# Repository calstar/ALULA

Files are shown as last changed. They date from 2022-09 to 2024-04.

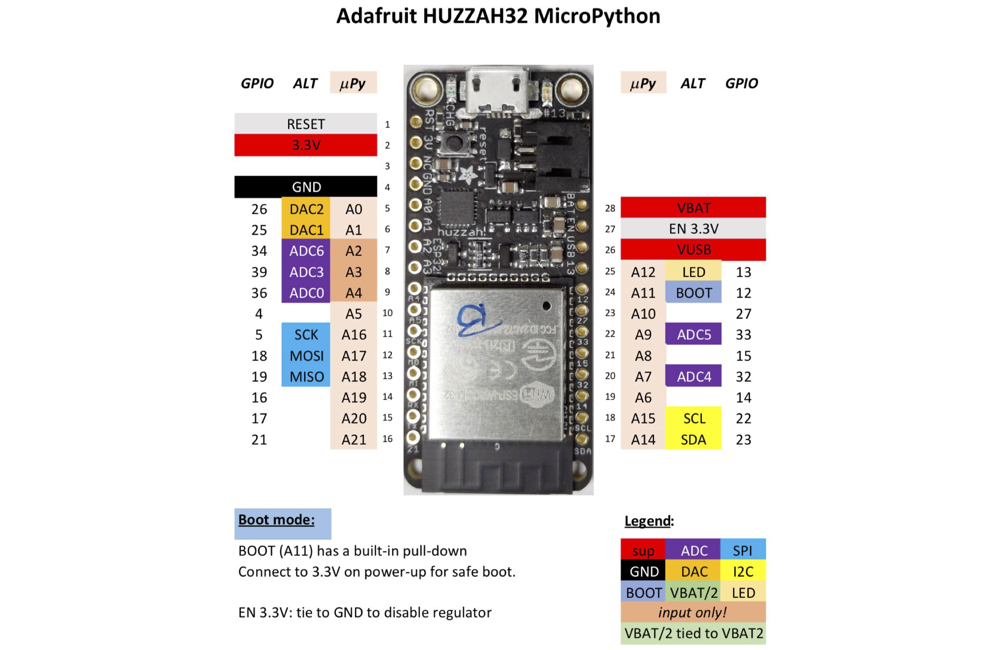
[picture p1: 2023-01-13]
esp32-huzzah-pinout.png

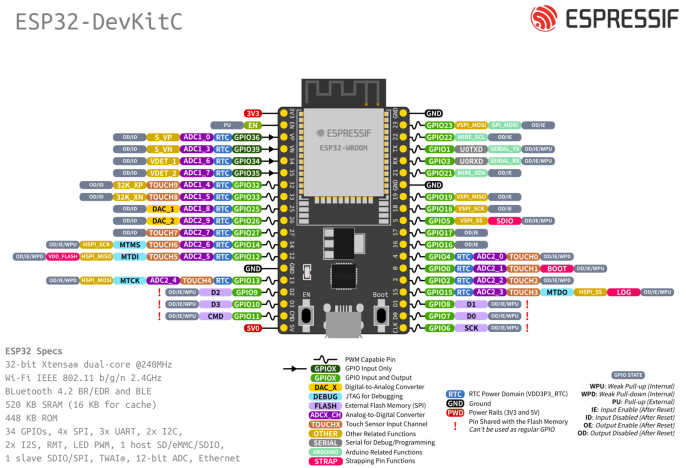
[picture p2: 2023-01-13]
SPRING-HOTFIRE-HARDWARE/le2_pcb/esp32-devkitC-v4-pinout.png

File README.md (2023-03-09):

# ALULA (LE2)
 Alula/ LE2 Hot-fire and Flight Vehicle Electronics Control

## Summary
**DAQboard.ino** file commands the ESP32 that reads data from sensors and commands from the COM Board, and sends data in a package to the COM Board.

**COMBoard.ino** file commands the ESP32 that receives data in a package from the DAQ  Board, sends commands to the DAQ Board, and sends data to MATLAB for plotting and data-saving purposes through the serial port.

**liveplot.m** is a MATLAB file that can receive data from the COM Board, create live plots, and save the data.
  1. **Change the test file name according to the trial number in the liveplot.m file.**
  2. Click "Run" to start the code, and close the plotting window to stop the code. Test data will be automatically stored in a spreadsheet under a folder called "**Test_Data_yyyy-mm-dd**."

## ESP32 MAC Addresses
- DAQ Breadboard:{0x24, 0x62, 0xAB, 0xD2, 0x85, 0xDC}
- COM Breadboard:{0xC4, 0xDD, 0x57, 0x9E, 0x91, 0x6C};
- DAQ Protoboard:

## Software requirement
**Ctrl click (Windows) or Cmd click the following links to open them in new tabs**
1. Arduino (https://www.arduino.cc/en/software)
2. MATLAB (https://software.berkeley.edu/matlab®)
    - To control the serial port, you need to install the [**Instrument Control Toolbox**](https://www.mathworks.com/products/instrument.html).
3. (optional) An external code editing software such as Atom (https://atom.io) or Visual Studio (https://visualstudio.microsoft.com/downloads/).
    - Arduino IDE and MATLAB are sufficient for all the coding
4. (recommended) GitHub Desktop (https://desktop.github.com). You can pull, push, and edit files with ease. **Step 3 required if you would like to download GitHub Desktop as the software requires an external editor.**

## How to contribute

### Using Git (recommended)
CLONE USING: 
```git clone --recurse-submodules git@github.com:calstar/LE2.git``` 

Please refer to https://rocketry.gitbook.io/public/tutorials/avionics/git-and-workflow for more information.

A basic workflow might go as follows:

`git status` 

`git add .` 

`git status` Note: if you see files here that are not code/hardware and should not be added (binaries, images, autosave files, etc.), STOP and fix the `.gitignore` 

`git commit -m "[Descriptive commit message of what you changed]"` 

`git push` 

### Using Github Desktop (not recommended)
1. Make sure you have access to this project
    - Check with you administrators
2. Go to the Github app, sign in, and click on the top left corner. You should see a pop-up window with an "Add" button. Select that button and choose "Clone repository."
3. Search in "Filter you repositories" using the keyword "ellie-ground." Select the correct repository and click "Clone."
    - If you want this cloned repository to be in a different folder, change the "Local Path."
4. After you have edited and saved the file in the local repository, GitHub Desktop will detect changes and prompt you to commit. Make sure to double check your changes before committing.
5. On the bottom left corner, put down a short summary that describes what you have changed, then click "Commit to **main**."
6. In the middle of the screen (or on the top banner) you will see "Push commits to the origin remote." If you are sure that the commit is ready, click "Push origin."
6. Check the project online and see if the changes have been reflected.

## Helpful resources
### ESP32-DevkitC/ ESP32-Devkit-v4 (for PCB application - antenna sticks out of board)
Getting started

https://docs.espressif.com/projects/esp-idf/en/latest/esp32/hw-reference/esp32/get-started-devkitc.html

Pinout reference

![esp32 devkitC pinout](https://github.com/calstar/ellie-ground/blob/main/Misc_resources/esp32-devkitC-v4-pinout.png?raw=true "ESP32 DevkitC Pinout")

### ESP32-WROOM/ ESP32-Devkit-v1 (for breadboard/protoboard application - antenna does NOT stick out of board)

Pinout reference
![esp32 wroom pinout](https://www.mischianti.org/wp-content/uploads/2020/11/ESP32-DOIT-DEV-KIT-v1-pinout-mischianti.png)

### ESP32-HUZZAH (for breadboard/protoboard application)

Pinout reference
![esp32 devkitC pinout](https://github.com/calstar/ellie-ground/blob/main/Misc_resources/esp32-huzzah-pinout.png?raw=true "ESP32 HUZZAH Pinout")

### Pressure transducer color code
Red - E+

Black - E-

Green - A-

White - A+

Other possible combinations: Blue E+; Red E-; Green A-; Black A+

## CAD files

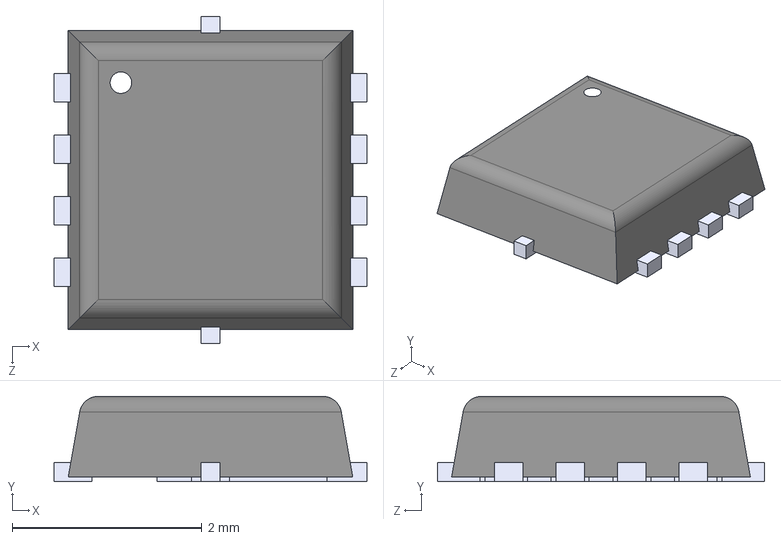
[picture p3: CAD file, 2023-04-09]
SPRING-HOTFIRE-HARDWARE/hotfire_pcbs/CSD25402Q3AT/CSD25402Q3AT.step
3.30 x 0.9 x 3.45 mm

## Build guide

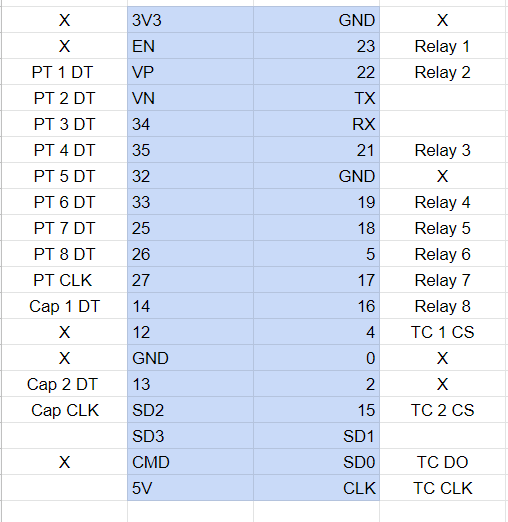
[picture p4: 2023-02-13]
SPRING-HOTFIRE-HARDWARE/le2_pcb/PROTOBOARDS/Core Board Setup.png

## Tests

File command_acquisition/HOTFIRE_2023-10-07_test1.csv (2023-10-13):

load:0x3fff0030,len:1344
load:0x40078000,len:13964
load:0x40080400,len:3600
entry | 0x400805f0
Start | of | Setup
274 | -1.00 | -1.00 | -1.00 | 0.00 | -1.00 | -1.00 | -1.00 | -1.00 | -1.00 | -1.00 | 0 | 0 | 1
526 | -1.00 | -1.00 | -1.00 | 0.00 | -1.00 | -1.00 | -1.00 | -1.00 | -1.00 | -1.00 | 0 | 0 | 1
777 | -1.00 | -1.00 | -1.00 | 0.00 | -1.00 | -1.00 | -1.00 | -1.00 | -1.00 | -1.00 | 0 | 0 | 1
1030 | -1.00 | -1.00 | -1.00 | 0.00 | -1.00 | -1.00 | -1.00 | -1.00 | -1.00 | -1.00 | 0 | 0 | 1
1283 | -1.00 | -1.00 | -1.00 | 0.00 | -1.00 | -1.00 | -1.00 | -1.00 | -1.00 | -1.00 | 0 | 0 | 1
1534 | -1.00 | -1.00 | -1.00 | 0.00 | -1.00 | -1.00 | -1.00 | -1.00 | -1.00 | -1.00 | 0 | 0 | 1
1787 | -1.00 | -1.00 | -1.00 | 0.00 | -1.00 | -1.00 | -1.00 | -1.00 | -1.00 | -1.00 | 0 | 0 | 1
2039 | -1.00 | -1.00 | -1.00 | 0.00 | -1.00 | -1.00 | -1.00 | -1.00 | -1.00 | -1.00 | 0 | 0 | 1
2290 | -1.00 | -1.00 | -1.00 | 0.00 | -1.00 | -1.00 | -1.00 | -1.00 | -1.00 | -1.00 | 0 | 0 | 1
2543 | -1.00 | -1.00 | -1.00 | 0.00 | -1.00 | -1.00 | -1.00 | -1.00 | -1.00 | -1.00 | 0 | 0 | 1
2795 | -1.00 | -1.00 | -1.00 | 0.00 | -1.00 | -1.00 | -1.00 | -1.00 | -1.00 | -1.00 | 0 | 0 | 1
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

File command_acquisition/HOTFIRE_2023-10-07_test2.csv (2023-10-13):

d:0x3fff0030,len:1344
entry | 0x400805f0
Start | of | Setup
283 | -1.00 | -1.00 | -1.00 | 0.00 | -1.00 | -1.00 | -1.00 | -1.00 | -1.00 | -1.00 | 0 | 0 | 1
535 | -1.00 | -1.00 | -1.00 | 0.00 | -1.00 | -1.00 | -1.00 | -1.00 | -1.00 | -1.00 | 0 | 0 | 1
787 | -1.00 | -1.00 | -1.00 | 0.00 | -1.00 | -1.00 | -1.00 | -1.00 | -1.00 | -1.00 | 0 | 0 | 1
1040 | -1.00 | -1.00 | -1.00 | 0.00 | -1.00 | -1.00 | -1.00 | -1.00 | -1.00 | -1.00 | 0 | 0 | 1
1291 | -1.00 | -1.00 | -1.00 | 0.00 | -1.00 | -1.00 | -1.00 | -1.00 | -1.00 | -1.00 | 0 | 0 | 1
1544 | -1.00 | -1.00 | -1.00 | 0.00 | -1.00 | -1.00 | -1.00 | -1.00 | -1.00 | -1.00 | 0 | 0 | 1
1795 | -1.00 | -1.00 | -1.00 | 0.00 | -1.00 | -1.00 | -1.00 | -1.00 | -1.00 | -1.00 | 0 | 0 | 1
2048 | -1.00 | -1.00 | -1.00 | 0.00 | -1.00 | -1.00 | -1.00 | -1.00 | -1.00 | -1.00 | 0 | 0 | 1
2300 | -1.00 | -1.00 | -1.00 | 0.00 | -1.00 | -1.00 | -1.00 | -1.00 | -1.00 | -1.00 | 0 | 0 | 1
2520 | -1.00 | -1.00 | -1.00 | 0.00 | -1.00 | -1.00 | -1.00 | -1.00 | -1.00 | -1.00 | 1 | 1 | 1
2541 | -1.00 | -1.00 | -1.00 | 0.00 | -1.00 | -1.00 | -1.00 | -1.00 | -1.00 | -1.00 | 1 | 1 | 1
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

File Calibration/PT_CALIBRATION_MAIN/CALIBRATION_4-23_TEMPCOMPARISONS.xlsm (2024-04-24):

Reading 1 X | Reading 1 Y | Slope (m) | Intercept (c) | Reading 2 X | Reading 2 Y | Slope (m) | Intercept (c) | Reading 3 X | Reading 3 Y | Slope (m) | Intercept (c) | Reading 4 X | Reading 4 Y | Slope (m) | Intercept (c) | Reading 5 X | Reading 5 Y | Slope (m) | Intercept (c)
13520 | 200 | 0 | 0 | 29781 | 200 | 0 | 0 | 6459.5 | 200 | 0 | 0 | 14634.5 | 200 | 0 | 0 | 9688 | 200 | 0 | 0
19259.5 | 300 | 0.01742312 | -35.5605889 | 29810 | 300 | 3.448275862 | -102493.1034 | 9018.5 | 300 | 0.039077765 | -52.42282141 | 19737.5 | 300 | 0.019596316 | -86.78228493 | 12148 | 300 | 0.040650407 | -193.8211382
26413 | 400 | 0.015450348 | -4.848246505 | 29867 | 400 | 2.246212781 | -66680.56765 | 11634 | 400 | 0.038649541 | -49.28878906 | 25813 | 400 | 0.017846464 | -58.0298165 | 15070 | 400 | 0.037069853 | -156.0333356
4892 | 0 | 0.018617062 | -73.26627337 | 29850.5 | 0 | 0.348350819 | -10165.30344 | 2706.5 | 0 | 0.044694679 | -108.1820725 | 6656 | 0 | 0.020940657 | -124.9236092 | 5829 | 0 | 0.043414896 | -238.8338921
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

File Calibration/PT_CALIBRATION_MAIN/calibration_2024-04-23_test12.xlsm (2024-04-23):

Reading 1 X | Reading 1 Y | Slope (m) | Intercept (c) | Reading 2 X | Reading 2 Y | Slope (m) | Intercept (c) | Reading 3 X | Reading 3 Y | Slope (m) | Intercept (c) | Reading 4 X | Reading 4 Y | Slope (m) | Intercept (c) | Reading 5 X | Reading 5 Y | Slope (m) | Intercept (c) | Reading 6 X | Reading 6 Y | Slope (m) | Intercept (c)
6751.5 | 0 | 0 | 0 | 29406.5 | 0 | 0 | 0 | 3987.5 | 0 | 0 | 0 | 6604 | 0 | 0 | 0 | 5176.5 | 0 | 0 | 0 | -21.5 | 0 | 0 | 0
18438 | 200 | 0.01711376374 | -115.5435759 | 29403.5 | 200 | -66.66666667 | 1960433.333 | 8948 | 200 | 0.04031851628 | -160.7700837 | 16601 | 200 | 0.0200060018 | -132.1196359 | 10116 | 200 | 0.04048992813 | -209.596113 | -2.5 | 200 | 10.52631579 | 226.3157895
24685 | 300 | 0.01677772934 | -112.2602874 | 29401 | 300 | -54.94505495 | 1615752.747 | 11454.5 | 300 | 0.04019669112 | -160.1324322 | 21899 | 300 | 0.01966509696 | -128.9915112 | 12635 | 300 | 0.04025957414 | -208.1164189 | 2 | 300 | 12.10498125 | 255.4365292
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

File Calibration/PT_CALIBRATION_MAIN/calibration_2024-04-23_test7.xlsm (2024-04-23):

Reading 1 X | Reading 1 Y | Slope (m) | Intercept (c) | Reading 2 X | Reading 2 Y | Slope (m) | Intercept (c) | Reading 3 X | Reading 3 Y | Slope (m) | Intercept (c) | Reading 4 X | Reading 4 Y | Slope (m) | Intercept (c) | Reading 5 X | Reading 5 Y | Slope (m) | Intercept (c)
13520 | 200 | 0 | 0 | 29781 | 200 | 0 | 0 | 6459.5 | 200 | 0 | 0 | 14634.5 | 200 | 0 | 0 | 9688 | 200 | 0 | 0
19259.5 | 300 | 0.01742312 | -35.5605889 | 29810 | 300 | 3.448275862 | -102493.1034 | 9018.5 | 300 | 0.039077765 | -52.42282141 | 19737.5 | 300 | 0.019596316 | -86.78228493 | 12148 | 300 | 0.040650407 | -193.8211382
26413 | 400 | 0.015450348 | -4.848246505 | 29867 | 400 | 2.246212781 | -66680.56765 | 11634 | 400 | 0.038649541 | -49.28878906 | 25813 | 400 | 0.017846464 | -58.0298165 | 15070 | 400 | 0.037069853 | -156.0333356
4892 | 0 | 0.018617062 | -73.26627337 | 29850.5 | 0 | 0.348350819 | -10165.30344 | 2706.5 | 0 | 0.044694679 | -108.1820725 | 6656 | 0 | 0.020940657 | -124.9236092 | 5829 | 0 | 0.043414896 | -238.8338921
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

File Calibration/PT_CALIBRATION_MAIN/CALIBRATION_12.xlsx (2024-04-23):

Reading 1 X | Reading 1 Y | Slope (m) | Intercept (c) | Reading 2 X | Reading 2 Y | Slope (m) | Intercept (c) | Reading 3 X | Reading 3 Y | Slope (m) | Intercept (c) | Reading 4 X | Reading 4 Y | Slope (m) | Intercept (c) | Reading 5 X | Reading 5 Y | Slope (m) | Intercept (c) | Reading 6 X | Reading 6 Y | Slope (m) | Intercept (c)
6751.5 | 0 | 0 | 0 | 29406.5 | 0 | 0 | 0 | 3987.5 | 0 | 0 | 0 | 6604 | 0 | 0 | 0 | 5176.5 | 0 | 0 | 0 | -21.5 | 0 | 0 | 0
18438 | 200 | 0.01711376374 | -115.5435759 | 29403.5 | 200 | -66.66666667 | 1960433.333 | 8948 | 200 | 0.04031851628 | -160.7700837 | 16601 | 200 | 0.0200060018 | -132.1196359 | 10116 | 200 | 0.04048992813 | -209.596113 | -2.5 | 200 | 10.52631579 | 226.3157895
24685 | 300 | 0.01677772934 | -112.2602874 | 29401 | 300 | -54.94505495 | 1615752.747 | 11454.5 | 300 | 0.04019669112 | -160.1324322 | 21899 | 300 | 0.01966509696 | -128.9915112 | 12635 | 300 | 0.04025957414 | -208.1164189 | 2 | 300 | 12.10498125 | 255.4365292
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

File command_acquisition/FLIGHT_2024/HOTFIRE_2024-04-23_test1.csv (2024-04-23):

Start | of | Setup
24:DC:C3:4B:61:E0
My | MAC | Address | 24:DC:C3:4B:61:E0
222 | -34.80 | -73.82 | -169.72 | -108.06 | 13.93 | -1.00 | 0.00 | 0.00 | 0.00 | 0.00 | False | False | False | False | Idle | Idle | QD | 40 | False
339 | -33.49 | -73.53 | -169.43 | -108.06 | 13.93 | -1.00 | 0.00 | 0.00 | 0.00 | 0.00 | False | False | False | False | Idle | Idle | QD | 40 | False
465 | -32.19 | -73.39 | -169.43 | -108.06 | 13.93 | -1.00 | 0.00 | 0.00 | 0.00 | 0.00 | False | False | False | False | Idle | Idle | Idle | 40 | False
713 | -32.19 | -73.39 | -169.43 | -108.06 | 13.93 | -1.00 | 0.00 | 0.00 | 0.00 | 0.00 | False | False | False | False | Idle | Idle | Idle | 40 | False
942 | -32.19 | -73.39 | -169.43 | -108.06 | 13.77 | -1.00 | 0.00 | 0.00 | 0.00 | 0.00 | False | False | False | False | Idle | Idle | Idle | 40 | False
1183 | -33.49 | -73.39 | -169.72 | -108.16 | 13.77 | -1.00 | 0.00 | 0.00 | 0.00 | 0.00 | False | False | False | False | Idle | Idle | Idle | 40 | False
1434 | -33.49 | -73.82 | -169.76 | -108.16 | 13.77 | -1.00 | 0.00 | 0.00 | 0.00 | 0.00 | False | False | False | False | Idle | Idle | Idle | 40 | False
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

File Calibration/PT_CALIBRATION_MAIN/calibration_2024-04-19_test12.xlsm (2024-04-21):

Reading 1 X | Reading 1 Y | Slope (m) | Intercept (c) | Reading 2 X | Reading 2 Y | Slope (m) | Intercept (c) | Reading 3 X | Reading 3 Y | Slope (m) | Intercept (c) | Reading 4 X | Reading 4 Y | Slope (m) | Intercept (c) | Reading 5 X | Reading 5 Y | Slope (m) | Intercept (c)
344922.5 | 0 | 0 | 0 | 3594 | 0 | 0 | 0 | 3620.5 | 0 | 0 | 0 | 4272 | 0 | 0 | 0 | 3790 | 0 | 0 | 0
346050 | 0 | 0 | 0 | 3517 | 0 | 0 | 0 | 3591.5 | 0 | 0 | 0 | 4271 | 0 | 0 | 0 | 3756.5 | 0 | 0 | 0
348607 | 0 | 0 | 0 | 3540 | 0 | 0 | 0 | 3601.5 | 0 | 0 | 0 | 4252 | 0 | 0 | 0 | 3803.5 | 0 | 0 | 0
7611491 | 140 | 1.927056557e-05 | -6.677755339 | 7701.5 | 140 | 0.03371730688 | -119.6992186 | 6593.5 | 140 | 0.04683537395 | -168.8158386 | 6907 | 140 | 0.0529875881 | -225.9903652 | 7754.5 | 140 | 0.03525063297 | -133.3614294
8388607 | 270 | 2.738601959e-05 | -11.32978836 | 11828 | 270 | 0.03275560395 | -115.716101 | 9498.5 | 270 | 0.04594229053 | -165.2200596 | 9391 | 270 | 0.05271510913 | -224.728134 | 11688.5 | 270 | 0.0342932607 | -129.1984753
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

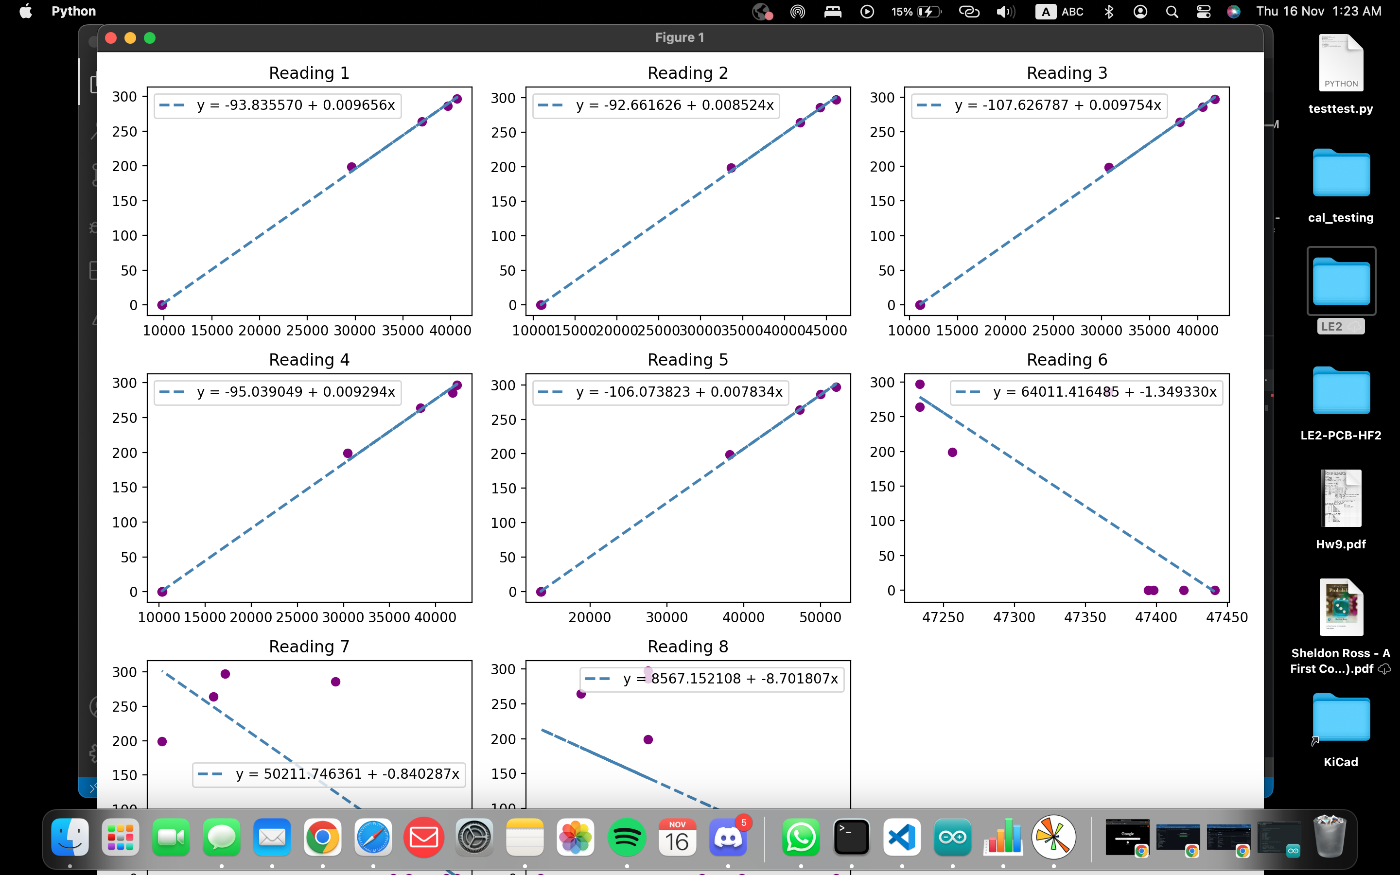
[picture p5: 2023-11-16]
Calibration/PT_CALIBRATION_MAIN/11-16-2023_PT_calibration/2023-11-16_HX2_C1.png

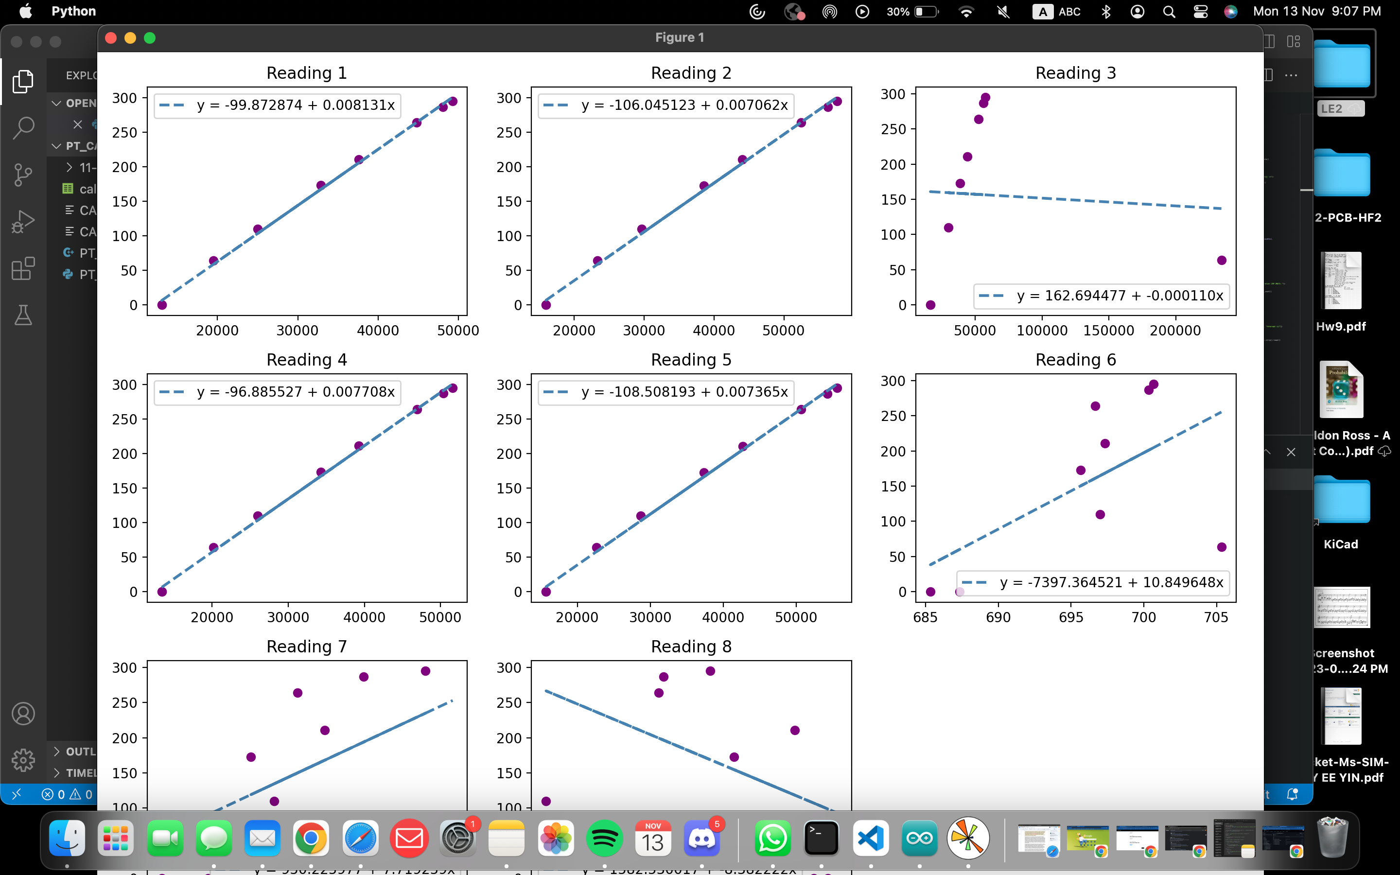
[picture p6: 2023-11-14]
Calibration/PT_CALIBRATION_MAIN/11_13_2023_PT_calibration/2023-11-13_HX1_C2_test1.png

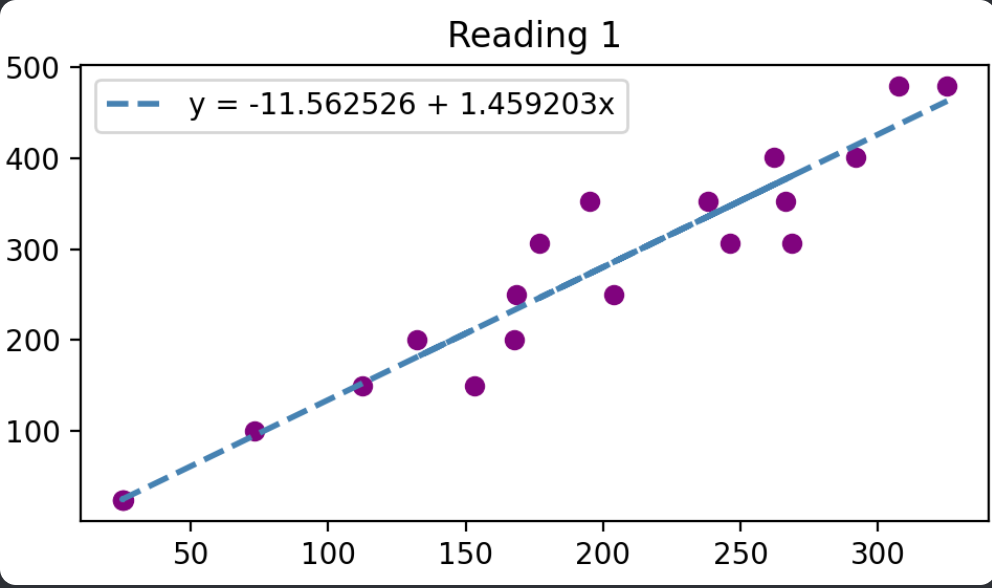
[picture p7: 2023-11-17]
Calibration/TC_Calibration/11-15-2023_TC_cal_C1/TC1.png

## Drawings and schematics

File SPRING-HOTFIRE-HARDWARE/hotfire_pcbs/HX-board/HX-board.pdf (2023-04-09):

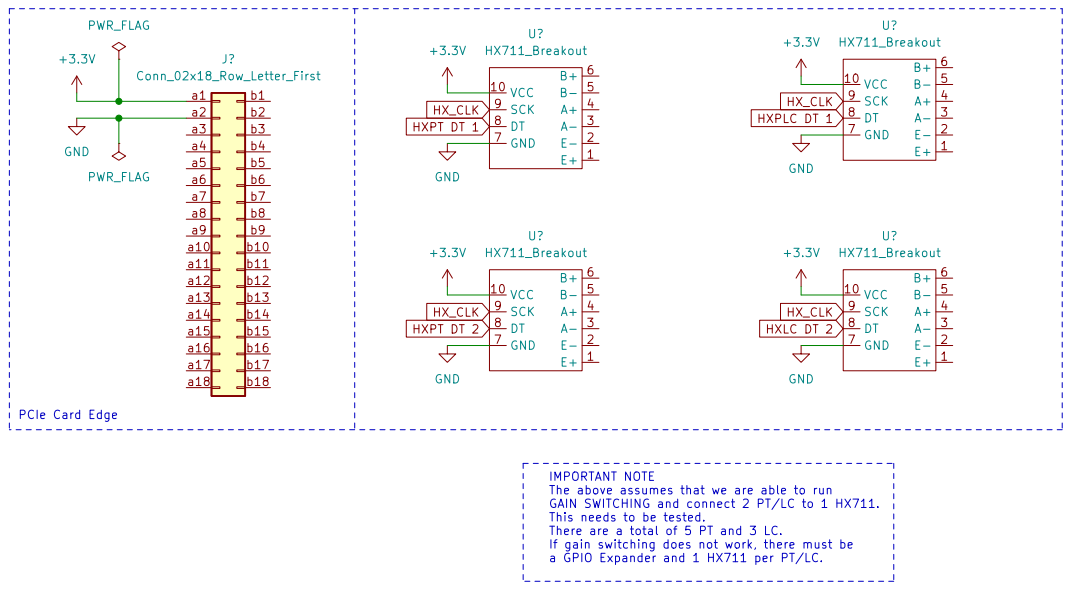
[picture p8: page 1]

IMPORTANT NOTE
The above assumes that we are able to run GAIN SWITCHING and connect 2 PT/LC to 1 HX711. This needs to be tested. There are a total of 5 PT and 3 LC.

If gain switching does not work, there must be
a GPIO Expander and 1 HX711 per PT/LC.

File: HX-board.kicad_sch Sheet: /
Id: 1/1 Title:

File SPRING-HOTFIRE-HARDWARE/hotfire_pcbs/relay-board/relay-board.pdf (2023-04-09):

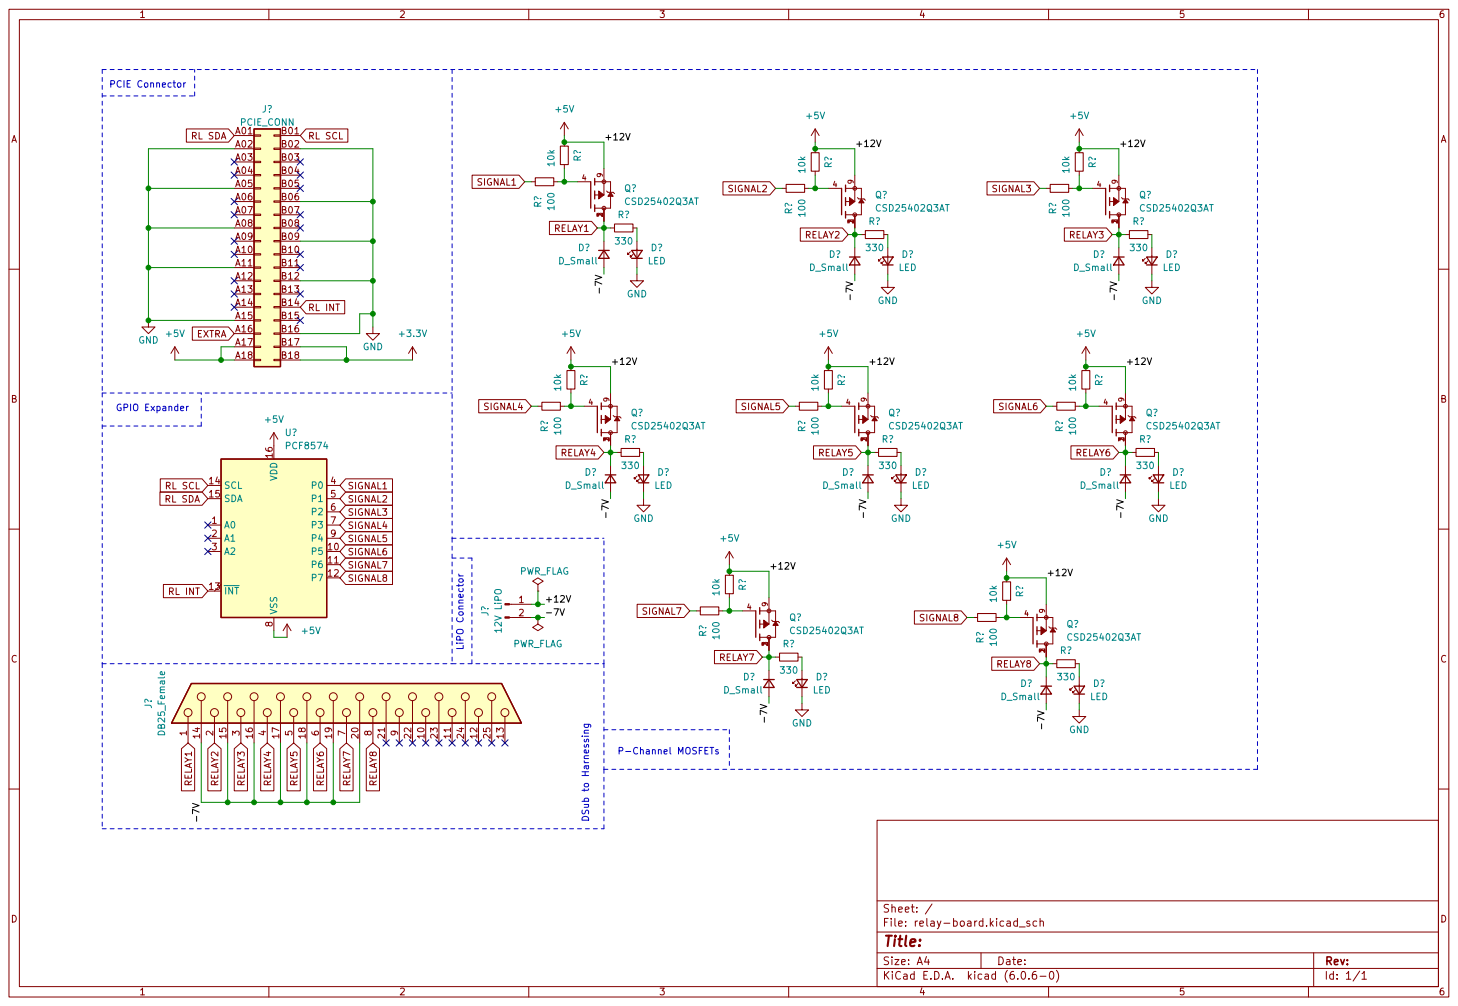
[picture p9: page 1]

RL INT RL SDA

File: relay-board.kicad_sch Sheet: / 123

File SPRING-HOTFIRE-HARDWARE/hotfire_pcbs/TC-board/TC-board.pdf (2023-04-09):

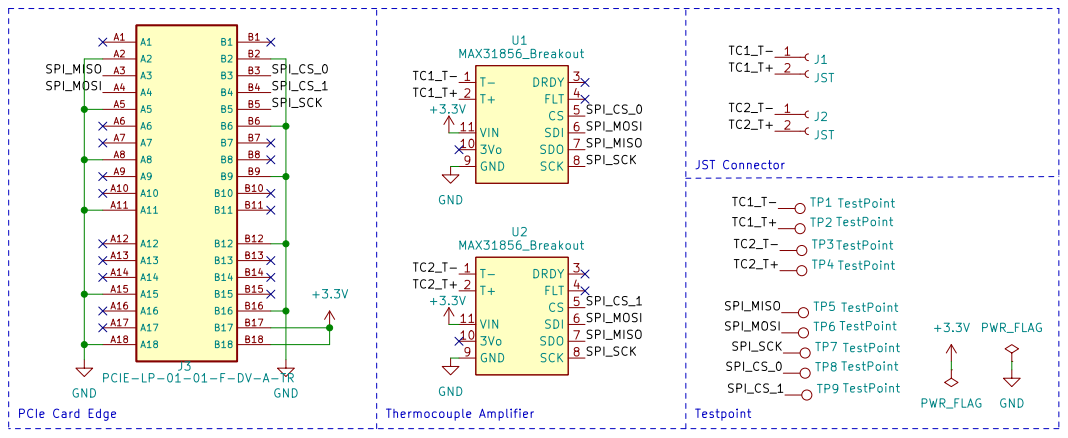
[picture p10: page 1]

TP1 TestPoint TP4 TestPoint TP5 TestPoint TP9 TestPoint +3.3V

File: TC-board.kicad_sch Sheet: / GND

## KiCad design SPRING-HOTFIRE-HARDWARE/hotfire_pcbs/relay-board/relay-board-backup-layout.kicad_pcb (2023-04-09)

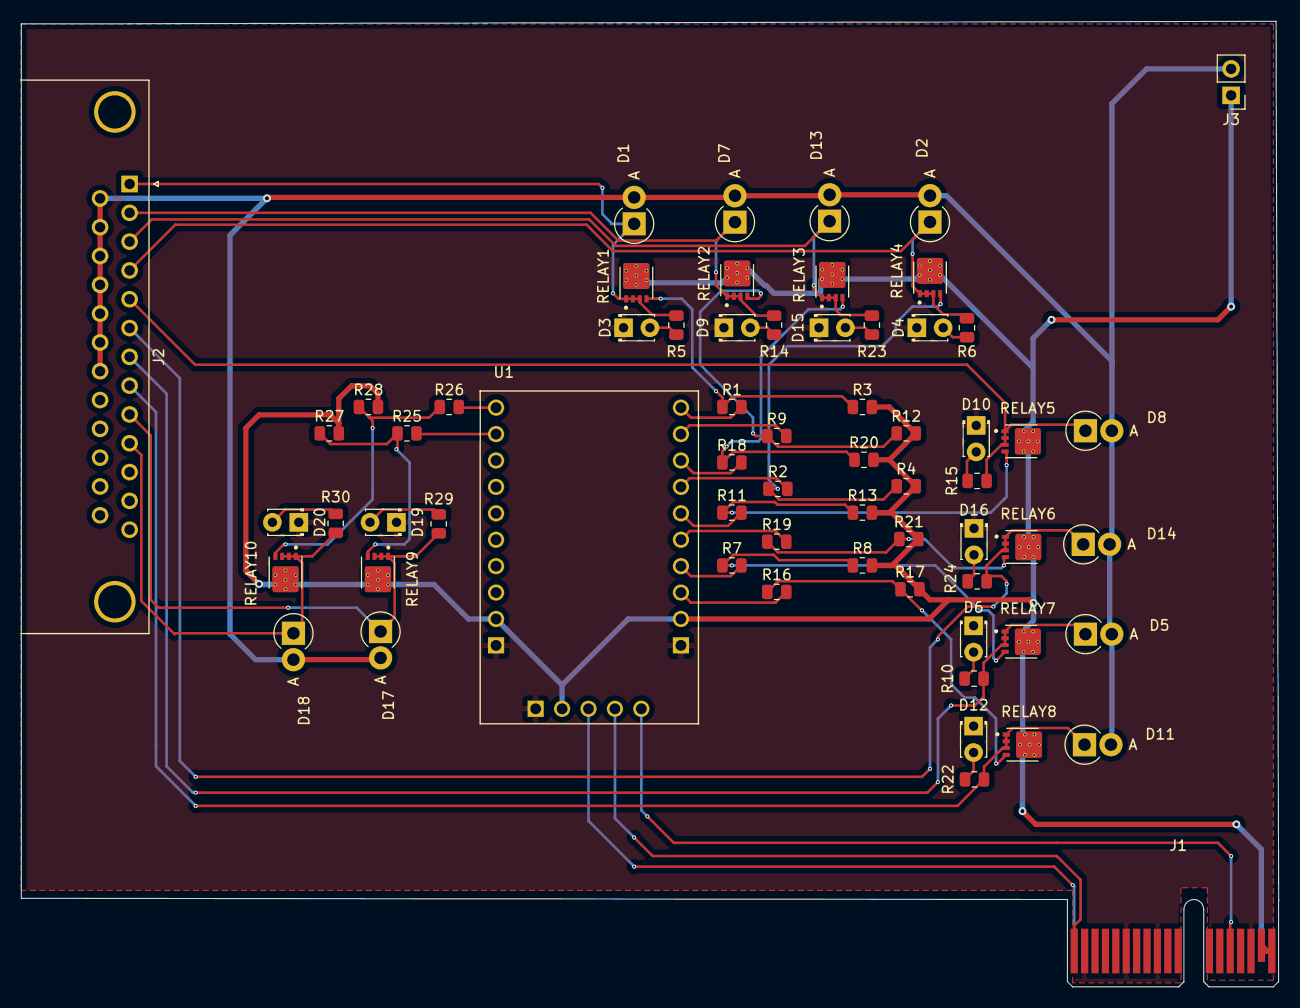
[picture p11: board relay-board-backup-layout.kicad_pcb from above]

Board: 2 copper layers, 120.9 x 92.8 mm, 64 parts (0 on the bottom side), 47 nets.

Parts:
D1, D2, D5, D7, D8, D11, D13, D14, D17, D18: D_Small; D_DO-15_P2.54mm_Vertical_AnodeUp
D3, D4, D6, D9, D10, D12, D15, D16, D19, D20: LED; LED_D1.8mm_W3.3mm_H2.4mm
J1: PCIE_CONN; BUS_PCIexpress_x1
J2: DB25_Female; DSUB-25_Male_Horizontal_P2.77x2.84mm_EdgePinOffset7.70mm_Ho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
J3: 12V LiPO; PinHeader_1x02_P2.54mm_Vertical
R1, R2, R7, R9, R11, R16, R18, R19, R25, R26: 100; R_0805_2012Metric
R3, R4, R8, R12, R13, R17, R20, R21, R27, R28: 10k; R_0805_2012Metric
R5, R6, R10, R14, R15, R22, R23, R24, R29, R30: 330; R_0805_2012Metric
RELAY1, RELAY2, RELAY3, RELAY4, RELAY5, RELAY6, RELAY7, RELAY8, RELAY9, RELAY10: CSD25402Q3AT; TRANS_CSD25402Q3AT
U1: PCF8575_Breakout

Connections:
+3.3V: J1.B17 (Pin_b17), J1.B18 (Pin_b18)
+5V: J1.A17 (Pin_a17), J1.A18 (Pin_a18), J3.1, R3.2, R4.2, R8.2, R12.2, R13.2, R17.2, R20.2, R21.2, R27.2, R28.2, RELAY1.9, RELAY1.9_1, RELAY1.9_2, RELAY1.9_3, RELAY1.9_4, RELAY1.9_5, RELAY1.9_6, RELAY1.9_7, RELAY2.9, RELAY2.9_1, RELAY2.9_2, RELAY2.9_3, RELAY2.9_4, RELAY2.9_5, RELAY2.9_6, RELAY2.9_7, RELAY3.9, RELAY3.9_1, RELAY3.9_2, RELAY3.9_3, RELAY3.9_4, RELAY3.9_5, RELAY3.9_6, RELAY3.9_7, RELAY4.9, RELAY4.9_1, RELAY4.9_2, RELAY4.9_3, RELAY4.9_4, RELAY4.9_5, RELAY4.9_6, RELAY4.9_7, RELAY5.9, RELAY5.9_1, RELAY5.9_2, RELAY5.9_3, RELAY5.9_4, RELAY5.9_5, RELAY5.9_6, RELAY5.9_7, RELAY6.9, RELAY6.9_1, RELAY6.9_2, RELAY6.9_3, RELAY6.9_4, RELAY6.9_5, RELAY6.9_6, RELAY6.9_7, RELAY7.9, RELAY7.9_1, RELAY7.9_2, RELAY7.9_3, RELAY7.9_4, RELAY7.9_5, RELAY7.9_6, RELAY7.9_7, RELAY8.9, RELAY8.9_1, RELAY8.9_2, RELAY8.9_3, RELAY8.9_4, RELAY8.9_5, RELAY8.9_6, RELAY8.9_7, RELAY9.9, RELAY9.9_1, RELAY9.9_2, RELAY9.9_3, RELAY9.9_4, RELAY9.9_5, RELAY9.9_6, RELAY9.9_7, RELAY10.9, RELAY10.9_1, RELAY10.9_2, RELAY10.9_3, RELAY10.9_4, RELAY10.9_5, RELAY10.9_6, RELAY10.9_7, U1.9 (VDD), U1.12 (VCC), U1.17 (VDD)
/-7V: D1.2 (A), D2.2 (A), D5.2 (A), D7.2 (A), D8.2 (A), D11.2 (A), D13.2 (A), D14.2 (A), D17.2 (A), D18.2 (A), J2.14, J2.15, J2.16, J2.17, J2.18, J2.19, J2.20, J2.21, J2.22, J3.2
GND: D3.1 (K), D4.1 (K), D6.1 (K), D9.1 (K), D10.1 (K), D12.1 (K), D15.1 (K), D16.1 (K), D19.1 (K), D20.1 (K), J1.A2 (Pin_a2), J1.A5 (Pin_a5), J1.A8 (Pin_a8), J1.A11 (Pin_a11), J1.A15 (Pin_a15), J1.B2 (Pin_b2), J1.B6 (Pin_b6), J1.B9 (Pin_b9), J1.B12 (Pin_b12), J1.B16 (Pin_b16), U1.10 (GND), U1.11 (GND), U1.16 (GND)
unnamed: D3.2 (A), R5.2
unnamed: D4.2 (A), R6.2
unnamed: D6.2 (A), R10.2
unnamed: D9.2 (A), R14.2
unnamed: D10.2 (A), R15.2
unnamed: D12.2 (A), R22.2
unnamed: D15.2 (A), R23.2
unnamed: D16.2 (A), R24.2
unnamed: D19.2 (A), R29.2
unnamed: D20.2 (A), R30.2
unnamed: R1.1, R3.1, RELAY1.4
unnamed: R2.1, R4.1, RELAY4.4
unnamed: R7.1, R8.1, RELAY7.4
unnamed: R9.1, R12.1, RELAY2.4
unnamed: R11.1, R13.1, RELAY5.4
unnamed: R16.1, R17.1, RELAY8.4
unnamed: R18.1, R20.1, RELAY3.4
unnamed: R19.1, R21.1, RELAY6.4
unnamed: R25.1, R27.1, RELAY9.4
unnamed: R26.1, R28.1, RELAY10.4
RELAY1: D1.1 (K), J2.1, R5.1, RELAY1.1, RELAY1.2, RELAY1.3
RELAY2: D7.1 (K), J2.2, R14.1, RELAY2.1, RELAY2.2, RELAY2.3
RELAY3: D13.1 (K), J2.3, R23.1, RELAY3.1, RELAY3.2, RELAY3.3
RELAY4: D2.1 (K), J2.4, R6.1, RELAY4.1, RELAY4.2, RELAY4.3
RELAY5: D8.1 (K), J2.5, R15.1, RELAY5.1, RELAY5.2, RELAY5.3
RELAY6: D14.1 (K), J2.6, R24.1, RELAY6.1, RELAY6.2, RELAY6.3
RELAY7: D5.1 (K), J2.7, R10.1, RELAY7.1, RELAY7.2, RELAY7.3
RELAY8: D11.1 (K), J2.8, R22.1, RELAY8.1, RELAY8.2, RELAY8.3
RELAY9: D17.1 (K), J2.9, R29.1, RELAY9.1, RELAY9.2, RELAY9.3
RELAY10: D18.1 (K), J2.10, R30.1, RELAY10.1, RELAY10.2, RELAY10.3
RL INT: J1.B14 (Pin_b14), U1.15 (INT)
RL SCL: J1.B1 (Pin_b1), U1.14 (SCL)
RL SDA: J1.A1 (Pin_a1), U1.13 (SDA)
SIGNAL1: R1.2, U1.25 (P07)
SIGNAL2: R9.2, U1.24 (P06)
SIGNAL3: R18.2, U1.23 (P05)
SIGNAL4: R2.2, U1.22 (P04)
SIGNAL5: R11.2, U1.21 (P03)
SIGNAL6: R19.2, U1.20 (P02)
SIGNAL7: R7.2, U1.19 (P01)
SIGNAL8: R16.2, U1.18 (P00)
SIGNAL9: R25.2, U1.2 (P11)
SIGNAL10: R26.2, U1.1 (P10)

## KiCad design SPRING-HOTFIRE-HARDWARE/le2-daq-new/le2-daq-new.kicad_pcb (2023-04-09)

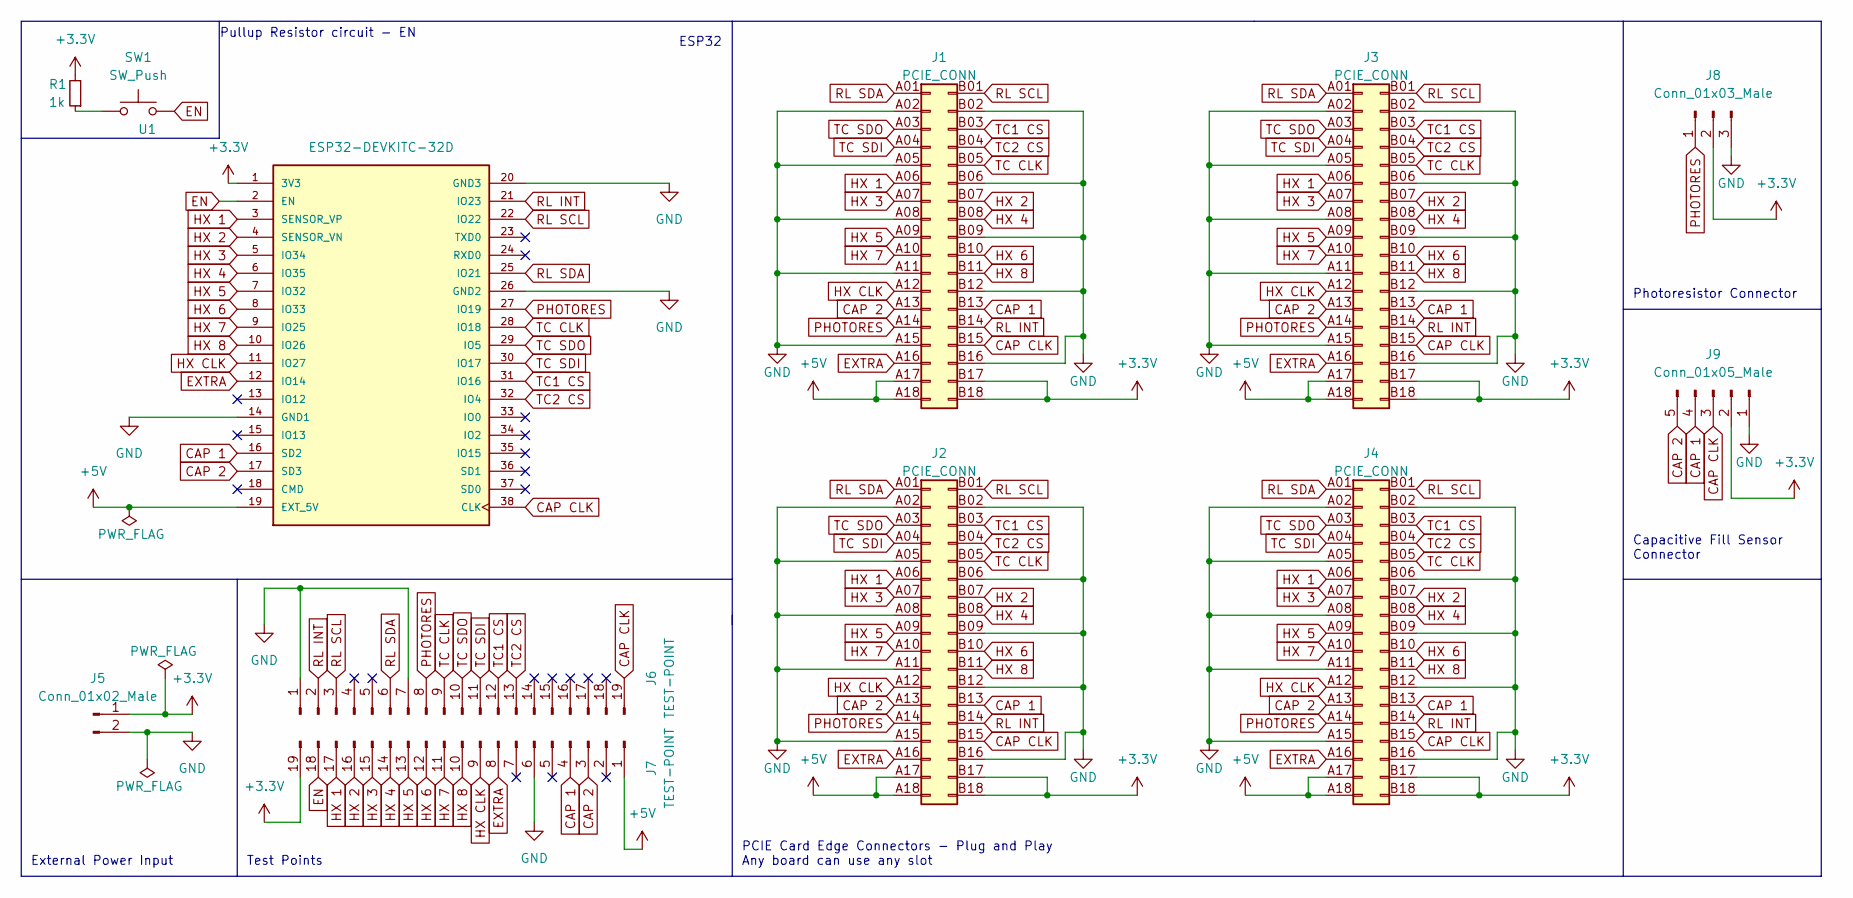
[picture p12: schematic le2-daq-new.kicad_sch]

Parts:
J1, J2, J3, J4: PCIE_CONN; AMPHENOL_10018784-10210TLF
J5: Conn_01x02_Male; PinHeader_1x02_P2.54mm_Vertical
J6, J7: TEST-POINT; PinHeader_1x19_P2.54mm_Vertical
J8: Conn_01x03_Male; PinHeader_1x03_P2.54mm_Vertical
J9: Conn_01x05_Male; PinHeader_1x05_P2.54mm_Vertical
R1: 1k; R_0805_2012Metric_Pad1.20x1.40mm_HandSolder
SW1: SW_Push; SolderJumper-2_P1.3mm_Bridged2Bar_Pad1.0x1.5mm
U1: ESP32-DEVKITC-32D; MODULE_ESP32-DEVKITC-32D; PARTREV 4

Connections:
+3.3V: J1.B17 (Pin_b17), J1.B18 (Pin_b18), J2.B17 (Pin_b17), J2.B18 (Pin_b18), J3.B17 (Pin_b17), J3.B18 (Pin_b18), J4.B17 (Pin_b17), J4.B18 (Pin_b18), J5.1, J7.19, J8.2, J9.2, R1.2, U1.1 (3V3)
+5V: J1.A17 (Pin_a17), J1.A18 (Pin_a18), J2.A17 (Pin_a17), J2.A18 (Pin_a18), J3.A17 (Pin_a17), J3.A18 (Pin_a18), J4.A17 (Pin_a17), J4.A18 (Pin_a18), J7.1, U1.19 (EXT_5V)
CAP 1: J1.B13 (Pin_b13), J2.B13 (Pin_b13), J3.B13 (Pin_b13), J4.B13 (Pin_b13), J7.4, J9.4, U1.16 (SD2)
CAP 2: J1.A13 (Pin_a13), J2.A13 (Pin_a13), J3.A13 (Pin_a13), J4.A13 (Pin_a13), J7.3, J9.5, U1.17 (SD3)
CAP CLK: J1.B15 (Pin_b15), J2.B15 (Pin_b15), J3.B15 (Pin_b15), J4.B15 (Pin_b15), J6.19, J9.3, U1.38 (CLK)
EN: J7.18, SW1.2, U1.2 (EN)
EXTRA: J1.A16 (Pin_a16), J2.A16 (Pin_a16), J3.A16 (Pin_a16), J4.A16 (Pin_a16), J7.8, U1.12 (IO14)
GND: J1.A02 (Pin_a2), J1.A05 (Pin_a5), J1.A08 (Pin_a8), J1.A11 (Pin_a11), J1.A15 (Pin_a15), J1.B02 (Pin_b2), J1.B06 (Pin_b6), J1.B09 (Pin_b9), J1.B12 (Pin_b12), J1.B16 (Pin_b16), J2.A02 (Pin_a2), J2.A05 (Pin_a5), J2.A08 (Pin_a8), J2.A11 (Pin_a11), J2.A15 (Pin_a15), J2.B02 (Pin_b2), J2.B06 (Pin_b6), J2.B09 (Pin_b9), J2.B12 (Pin_b12), J2.B16 (Pin_b16), J3.A02 (Pin_a2), J3.A05 (Pin_a5), J3.A08 (Pin_a8), J3.A11 (Pin_a11), J3.A15 (Pin_a15), J3.B02 (Pin_b2), J3.B06 (Pin_b6), J3.B09 (Pin_b9), J3.B12 (Pin_b12), J3.B16 (Pin_b16), J4.A02 (Pin_a2), J4.A05 (Pin_a5), J4.A08 (Pin_a8), J4.A11 (Pin_a11), J4.A15 (Pin_a15), J4.B02 (Pin_b2), J4.B06 (Pin_b6), J4.B09 (Pin_b9), J4.B12 (Pin_b12), J4.B16 (Pin_b16), J5.2, J6.1, J6.7, J7.6, J8.3, J9.1, U1.14 (GND1), U1.20 (GND3), U1.26 (GND2)
HX 1: J1.A06 (Pin_a6), J2.A06 (Pin_a6), J3.A06 (Pin_a6), J4.A06 (Pin_a6), J7.17, U1.3 (SENSOR_VP)
HX 2: J1.B07 (Pin_b7), J2.B07 (Pin_b7), J3.B07 (Pin_b7), J4.B07 (Pin_b7), J7.16, U1.4 (SENSOR_VN)
HX 3: J1.A07 (Pin_a7), J2.A07 (Pin_a7), J3.A07 (Pin_a7), J4.A07 (Pin_a7), J7.15, U1.5 (IO34)
HX 4: J1.B08 (Pin_b8), J2.B08 (Pin_b8), J3.B08 (Pin_b8), J4.B08 (Pin_b8), J7.14, U1.6 (IO35)
HX 5: J1.A09 (Pin_a9), J2.A09 (Pin_a9), J3.A09 (Pin_a9), J4.A09 (Pin_a9), J7.13, U1.7 (IO32)
HX 6: J1.B10 (Pin_b10), J2.B10 (Pin_b10), J3.B10 (Pin_b10), J4.B10 (Pin_b10), J7.12, U1.8 (IO33)
HX 7: J1.A10 (Pin_a10), J2.A10 (Pin_a10), J3.A10 (Pin_a10), J4.A10 (Pin_a10), J7.11, U1.9 (IO25)
HX 8: J1.B11 (Pin_b11), J2.B11 (Pin_b11), J3.B11 (Pin_b11), J4.B11 (Pin_b11), J7.10, U1.10 (IO26)
HX CLK: J1.A12 (Pin_a12), J2.A12 (Pin_a12), J3.A12 (Pin_a12), J4.A12 (Pin_a12), J7.9, U1.11 (IO27)
unnamed: R1.1, SW1.1
PHOTORES: J1.A14 (Pin_a14), J2.A14 (Pin_a14), J3.A14 (Pin_a14), J4.A14 (Pin_a14), J6.8, J8.1, U1.27 (IO19)
RL INT: J1.B14 (Pin_b14), J2.B14 (Pin_b14), J3.B14 (Pin_b14), J4.B14 (Pin_b14), J6.2, U1.21 (IO23)
RL SCL: J1.B01 (Pin_b1), J2.B01 (Pin_b1), J3.B01 (Pin_b1), J4.B01 (Pin_b1), J6.3, U1.22 (IO22)
RL SDA: J1.A01 (Pin_a1), J2.A01 (Pin_a1), J3.A01 (Pin_a1), J4.A01 (Pin_a1), J6.6, U1.25 (IO21)
TC1 CS: J1.B03 (Pin_b3), J2.B03 (Pin_b3), J3.B03 (Pin_b3), J4.B03 (Pin_b3), J6.12, U1.31 (IO16)
TC2 CS: J1.B04 (Pin_b4), J2.B04 (Pin_b4), J3.B04 (Pin_b4), J4.B04 (Pin_b4), J6.13, U1.32 (IO4)
TC CLK: J1.B05 (Pin_b5), J2.B05 (Pin_b5), J3.B05 (Pin_b5), J4.B05 (Pin_b5), J6.9, U1.28 (IO18)
TC SDI: J1.A04 (Pin_a4), J2.A04 (Pin_a4), J3.A04 (Pin_a4), J4.A04 (Pin_a4), J6.11, U1.30 (IO17)
TC SDO: J1.A03 (Pin_a3), J2.A03 (Pin_a3), J3.A03 (Pin_a3), J4.A03 (Pin_a3), J6.10, U1.29 (IO5)

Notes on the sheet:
Capacitive Fill Sensor Connector
Pullup Resistor circuit - EN
Test Points
ESP32
Photoresistor Connector
External Power Input
PCIE Card Edge Connectors - Plug and Play Any board can use any slot

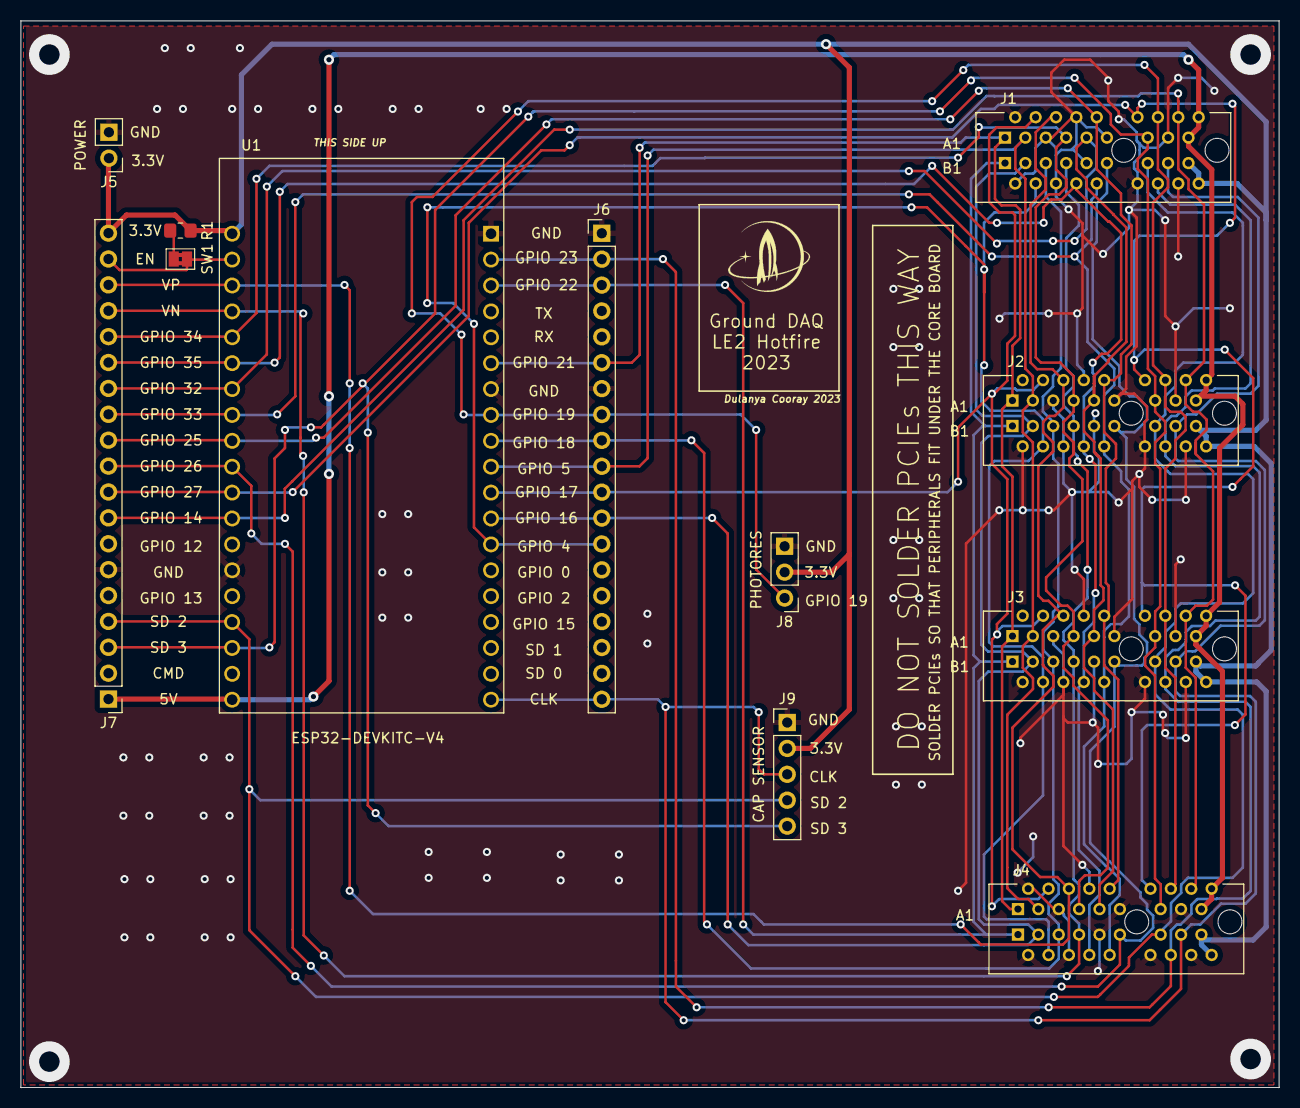
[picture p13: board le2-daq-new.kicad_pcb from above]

Board: 2 copper layers, 123.4 x 104.6 mm, 12 parts (0 on the bottom side), 27 nets.

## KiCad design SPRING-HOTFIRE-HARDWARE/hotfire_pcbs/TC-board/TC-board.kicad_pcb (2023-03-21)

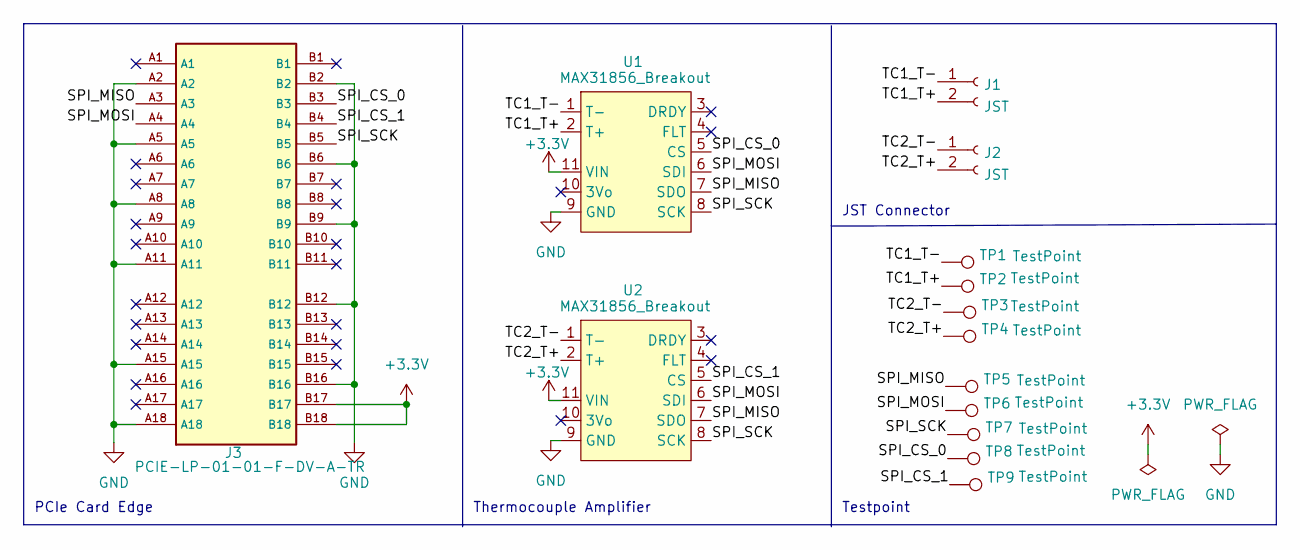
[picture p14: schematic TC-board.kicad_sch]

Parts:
J1, J2: JST; PinHeader_1x02_P2.54mm_Horizontal
J3: PCIE-LP-01-01-F-DV-A-TR; BUS_PCIexpress_x1; PARTREV B
TP1, TP2, TP3, TP4, TP5, TP6, TP7, TP8, TP9: TestPoint; TestPoint_Plated_Hole_D2.0mm
U1, U2: MAX31856_Breakout

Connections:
+3V3: J3.B17, J3.B18, U1.11 (VIN), U2.11 (VIN)
/SPI_CS_0: J3.B3, TP8.1, U1.5 (CS)
/SPI_CS_1: J3.B4, TP9.1, U2.5 (CS)
/SPI_MISO: J3.A3, TP5.1, U1.7 (SDO), U2.7 (SDO)
/SPI_MOSI: J3.A4, TP6.1, U1.6 (SDI), U2.6 (SDI)
/SPI_SCK: J3.B5, TP7.1, U1.8 (SCK), U2.8 (SCK)
/TC1_T+: J1.2, TP2.1, U1.2 (T+)
/TC1_T-: J1.1, TP1.1, U1.1 (T-)
/TC2_T+: J2.2, TP4.1, U2.2 (T+)
/TC2_T-: J2.1, TP3.1, U2.1 (T-)
GND: J3.A2, J3.A5, J3.A8, J3.A11, J3.A15, J3.A18, J3.B2, J3.B6, J3.B9, J3.B12, J3.B16, U1.9 (GND), U2.9 (GND)

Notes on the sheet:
Testpoint
JST Connector
PCIe Card Edge
Thermocouple Amplifier

Board: 2 copper layers, 14 parts (0 on the bottom side), 11 nets, no tracks yet.

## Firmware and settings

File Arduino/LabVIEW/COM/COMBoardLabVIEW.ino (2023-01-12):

#include <esp_now.h>
#include <WiFi.h>
#include <ESP32Servo.h>
#include <Wire.h>
#include <Arduino.h>
#include "HX711.h"


int servo1ClosedPosition = 100;
int servo1OpenPosition = 0;
int servo2ClosedPosition = 155;
int servo2OpenPosition = 20;
//EH VENT SEFRVO 1 =180

float pressTime = 0;
const int buttonpin1 = 19;
//const int buttonpin1 = 27;
const int buttonpin2 = 17;
const int igniterIndicator = 16;
const int firePin = 21; //SET PIN NUMBER BUTTON

const int pin6 = 4;
const int LEDpin = 23;
const int servo1Open = 22;//SET PIN NUMBER BASED ON SOLDERING//
const int servo2Open = 14;//SET PIN NUMBER BASED ON SOLDERING//
const int DAQIndicator = 25;//SET PIN NUMBER BASED ON SOLDERING//
const int COMIndicator = 5;//SET PIN NUMBER BASED ON SOLDERING//

String success;
int servo1_curr = servo1ClosedPosition;
int servo2_curr = servo2ClosedPosition;
float incomingS1 = 0;
float incomingS2 = 0;
float incomingPT1 = 0;
float incomingPT2 = 0;
float incomingPT3 = 0;
float incomingPT4 = 0;
float incomingFM = 0;
float incomingLC1 = 0;
float incomingLC2 = 0;
float incomingLC3 = 0;
esp_now_peer_info_t peerInfo;
bool pressed1 = false;
bool pressed2 = false;
bool pressed3 = false;

// SET FOR ACTIVE MODE //
bool hotfire = true;
//SET IF PLOTTING WITH MATLAB OR NOT. SERVO MANUAL CONTROL AND
//MATLAB PLOTTING ARE NOT COMPATIBLE DUE TO USING THE SAME SERIAL
//INPUT. IF TRUE, PLOTTING ENABLED. IF FALSE, MANUAL CONTROL ENABLED
bool MatlabPlot = false;


float button1Time = 0;
float currTime = 0;
float loopTime = 0;

float receiveTimeDAQ = 0;
float receiveTimeCOM = 0;

//for blinking LED during Data Collection
int x = 1;
unsigned long t1;
unsigned long t2;

int state = 0;
//

//DAQ Breadboard {0x24, 0x62, 0xAB, 0xD2, 0x85, 0xDC}
//DAQ Protoboard {0x0C, 0xDC, 0x7E, 0xCB, 0x05, 0xC4}
//NON BUSTED DAQ {0x7C, 0x9E, 0xBD, 0xD8, 0xFC, 0x14}
// uint8_t broadcastAddress[] = {0x7C, 0x9E, 0xBD, 0xD8, 0xFC, 0x14}; //change to new Mac Address

uint8_t broadcastAddress[] = {0x30, 0xC6, 0xF7, 0x2A, 0x28, 0x04};
//Structure example to send data
//Must match the receiver structure
typedef struct struct_message {
    float pt1;
    float pt2;
    float pt3;
    float pt4;
    float lc1;
    float lc2;
    float lc3;
    float fm;
    int S1;
    int S2;
    int S1S2;
    boolean I;
} struct_message;

// Create a struct_message called Readings to recieve sensor readings remotely
struct_message incomingReadings;

// Create a struct_message to send commands
struct_message Commands;

//
void OnDataSent(const uint8_t *mac_addr, esp_now_send_status_t status) {
 // Serial.print("\r\nLast Packet Send Status:\t");
 Serial.println(status == ESP_NOW_SEND_SUCCESS ? "Delivery Success" : "Delivery Fail");
  if (status == 0){
    success = "Delivery Success :)";
    digitalWrite(DAQIndicator, HIGH);
    receiveTimeDAQ = millis();
  }
  else{
    success = "Delivery Fail :(";
    digitalWrite(DAQIndicator, LOW);
  }

}

void OnDataRecv(const uint8_t * mac, const uint8_t *incomingData, int len) {
  memcpy(&incomingReadings, incomingData, sizeof(incomingReadings));
 Serial.print("Bytes received: ");
  Serial.println(len);
  incomingPT1 = incomingReadings.pt1;
  incomingPT2 = incomingReadings.pt2;
  incomingPT3 = incomingReadings.pt3;
  incomingPT4 = incomingReadings.pt4;
  incomingFM = incomingReadings.fm;
  incomingLC1 = incomingReadings.lc1;
  incomingLC2 = incomingReadings.lc2;
  incomingLC3 = incomingReadings.lc3;
  incomingS1 = incomingReadings.S1;
  incomingS2 = incomingReadings.S2;
  digitalWrite(COMIndicator, HIGH);
  receiveTimeCOM = millis();
  Serial.println("Data received");

}

void setup() {
  Commands.S1 = servo1ClosedPosition;
  Commands.S2 = servo2ClosedPosition;
  // put your setup code here, to run once:
  Serial.begin(115200);
  pinMode(buttonpin1,INPUT);
  pinMode(buttonpin2, INPUT);
  pinMode(igniterIndicator,INPUT);
  pinMode(firePin, INPUT);

  pinMode(LEDpin, OUTPUT);
  pinMode(servo1Open, OUTPUT);
  pinMode(servo2Open, OUTPUT);
  pinMode(DAQIndicator, OUTPUT);
  pinMode(COMIndicator, OUTPUT);
  pinMode(pin6, OUTPUT);

  digitalWrite(LEDpin,LOW);
  digitalWrite(servo1Open, LOW);
  digitalWrite(servo2Open, LOW);
  digitalWrite(DAQIndicator, LOW);
  digitalWrite(COMIndicator, LOW);
  digitalWrite(pin6, LOW);


  //set device as WiFi station
  WiFi.mode(WIFI_STA);

  //initialize ESP32
   if (esp_now_init() != ESP_OK) {
    //Serial.println("Error initializing ESP-NOW");
    return;
  }
   // Once ESPNow is successfully Init, we will register for Send CB to
  // get the status of Trasnmitted packet
  esp_now_register_send_cb(OnDataSent);

  // Register peer
  memcpy(peerInfo.peer_addr, broadcastAddress, 6);
  peerInfo.channel = 0;
  peerInfo.encrypt = false;

  // Add peer
  if (esp_now_add_peer(&peerInfo) != ESP_OK){
    //Serial.println("Failed to add peer");
    return;
  }
  // Register for a callback function that will be called when data is received
  esp_now_register_recv_cb(OnDataRecv);

}


void loop() {
  // put your main code here, to run repeatedly:
  // STATES:
  // 0 = RESTING LED dark
  // 1 = ARMED LED Bright
  // 2 = ACTUATE VALVES ON PRE_SET PARAMETERS (IF USING MATLAB) LED Blinking
  //     READY FOR SERVO VALVE ANGLE INPUTS (IN FORM angle1,angle2)

  switch (state) {
    case 0:
//      Serial.println("State 0");
      //Serial.println("IN CASE 0");
      Commands.S1 = servo1ClosedPosition;
      Commands.S2 = servo2ClosedPosition;
      //Serial.println("State 0");

      digitalWrite(LEDpin, LOW);
      digitalWrite(pin6, LOW);
      //digitalWrite(servo1Open, HIGH);
      //digitalWrite(servo2Open, HIGH);
      pressed1 = digitalRead(buttonpin1);
      currTime = millis();
      if (pressed1 && ((currTime - button1Time) > 1000)) {
        state = 1;
        button1Time = currTime;
        // Serial.println("State 1");
        // Serial.println("BUTTON 1 GOOD");
      }
      if ((millis() - receiveTimeDAQ) > 50) {
        digitalWrite(DAQIndicator, LOW);
      }
      if ((millis() - receiveTimeCOM) > 50) {
        digitalWrite(COMIndicator, LOW);
      }
      break;
    case 1:
      //Serial.println("State 1");
      //Serial.println("IN CASE 1");
      digitalWrite(LEDpin, HIGH);
      //Serial.println("State 1");
      pressed2 = digitalRead(buttonpin2);
      pressed3 = digitalRead(buttonpin1);
      currTime = millis();
      if (pressed2) {
        if (hotfire) {
          state = 4;
        } else {
          state = 2;
      }
        // Serial.println("State 2");
      }
      if (pressed3 && ((currTime - button1Time) > 1000)) {
        button1Time = currTime;
        state = 0;
        // Serial.println("State 0");
      }
      if ((millis() - receiveTimeDAQ) > 50) {
        digitalWrite(DAQIndicator, LOW);
      }
      if ((millis() - receiveTimeCOM) > 50) {
        digitalWrite(COMIndicator, LOW);
      }
      break;
    case 2:
    //  Serial.println("State 2");
      //Serial.println("IN CASE 2");
      if (MatlabPlot) {
        Commands.S1 = 90 - servo1_curr;
        Commands.S2 = 90 - servo2_curr;
        servo1_curr = 90 - servo1_curr;
        servo2_curr = 90 - servo2_curr;
        pressTime = millis();
        digitalWrite(pin6, HIGH);

        while (millis() - pressTime <= 5000) {

          t2=millis();
          if (t2-t1 >=100){
              x=1-x;
              t1=millis();
              digitalWrite(LEDpin,x);
              // Serial.print(t1);
            }

          pressed3 = digitalRead(buttonpin1);
          if (pressed3) {
            state = 0;
            break;
          }
          if (state == 3) {
            break;
          }
          if ((millis() - receiveTimeDAQ) > 50) {
            digitalWrite(DAQIndicator, LOW);
          }
          if ((millis() - receiveTimeCOM) > 50) {
            digitalWrite(COMIndicator, LOW);
          }

          if ((millis() - loopTime) >= 50) {
            esp_err_t result = esp_now_send(broadcastAddress, (uint8_t *) &Commands, sizeof(Commands));
            if (result != ESP_OK) {
              break;
            // Serial.println("Sent with success");
            }
            //else {
              //Serial.println("Error sending the data");
            //}
            loopTime = millis();
           // Serial.print(loopTime);
           // Serial.print(" ");
            // Print the flow rate for this second in litres / minute
            // Serial.print("Flow rate: ");
            //Serial.print(incomingFM);  // Print the integer part of the variable
            //Serial.print("L/min");
            //Serial.print(" ");       // Print tab space

           //PT TEST
            //Serial.print("Output Pressures: ");
            Serial.print(incomingPT1);
            Serial.print(" ");
            Serial.print(incomingPT2);
            Serial.print(" ");
            Serial.print(incomingPT3);
            Serial.print(" ");
            Serial.print(incomingPT4);
            Serial.print(" ");
            Serial.print(incomingLC1);
            Serial.print(" ");
            //Serial.println("psi / ");

          //  Serial.print(" ");       // Print tab space

          // FM Test

            Serial.println(incomingFM);
            // Serial.print(" ");

            //Serial.println("Commands Follow");
            // Serial.print(Commands.S1);
            // Serial.print(" ");
            // Serial.println(Commands.S2);
             // Print the cumulative total of litres flowed since starting
            //Serial.print("Output Liquid Quantity: ");
             //Serial.print(totalMilliLitres);
             //Serial.print("mL / ");
             //Serial.print(totalMilliLitres / 1000);
             //Serial.print("L");
             //Serial.print("\t");       // Print tab space

           //LC TEST

           //Serial.print("Load Cell Stuff:");
           //Serial.print(incomingLC1);
           //Serial.print(incomingLC2);
           //Serial.print(incomingLC3);

           //delay(50); //delay of 50 optimal for recieving and transmitting
         }
        }

      } else {
        while (!Serial.available()) {
          pressed3 = digitalRead(buttonpin1);
          Serial.print(pressed3);
          delay(5);
          if ((millis() - receiveTimeDAQ) > 50) {
            digitalWrite(DAQIndicator, LOW);
          }
          if ((millis() - receiveTimeCOM) > 50) {
            digitalWrite(COMIndicator, LOW);
          }
          esp_err_t result = esp_now_send(broadcastAddress, (uint8_t *) &Commands, sizeof(Commands));
            if (result != ESP_OK) {
              break;
            // Serial.println("Sent with success");
            }
            //else {
              //Serial.println("Error sending the data");
            //}
          if (pressed3) {
            state = 0;
            // Serial.println("State 0");
            break;}  //waiting for inputs
          }
        String angles = Serial.readString();
        int index = angles.indexOf(",");
        String readAngle1 = angles.substring(0, index);
        String readAngle2 = angles.substring(index+1, angles.length());
        if (angles.length() >= 3) {
          Serial.println(readAngle1);
          Serial.println(readAngle2);
          Commands.S1 = readAngle1.toInt();
          Commands.S2 = readAngle2.toInt();
          if (Commands.S1 == servo1ClosedPosition) {
            digitalWrite(servo1Open, LOW);
          } else {
            digitalWrite(servo1Open, HIGH);
          }

          if (Commands.S2 == servo2ClosedPosition) {
            digitalWrite(servo2Open, LOW);
          } else {
            digitalWrite(servo2Open, HIGH);
          }
          esp_err_t result = esp_now_send(broadcastAddress, (uint8_t *) &Commands, sizeof(Commands));
          if (result != ESP_OK) {
              break;
            // Serial.println("Sent with success");
            }
            //else {
              //Serial.println("Error sending the data");
            //}

        }

      }
      break;
     case 3:
    //  Serial.println("State 3");
      Commands.S1 = servo1ClosedPosition;
      Commands.S2 = servo2ClosedPosition;
      digitalWrite(DAQIndicator, LOW);
      digitalWrite(COMIndicator, LOW);
      digitalWrite(servo1Open, LOW);
      digitalWrite(servo2Open, LOW);
      if ((millis() - receiveTimeDAQ) > 50) {
        digitalWrite(DAQIndicator, LOW);
      }
      if ((millis() - receiveTimeCOM) > 50) {
        digitalWrite(COMIndicator, LOW);
      }

      break;
    case 4:
      //Serial.println("State 4");
      digitalWrite(pin6, HIGH);
      if (digitalRead(igniterIndicator)) {
        Commands.S1S2 = 99;
        Commands.S1 = servo1ClosedPosition;
        Commands.S2 = servo2ClosedPosition;
        esp_err_t result = esp_now_send(broadcastAddress, (uint8_t *) &Commands, sizeof(Commands));
        if (result != ESP_OK) {
            break;
          // Serial.println("Sent with success");
          }
        state = 5;
      }
      if (digitalRead(buttonpin1)) {
        state = 0;
      }
      if ((millis() - receiveTimeDAQ) > 100) {
        digitalWrite(DAQIndicator, LOW);
      }
      if ((millis() - receiveTimeCOM) > 100) {
        digitalWrite(COMIndicator, LOW);
      }
      break;
    case 5:
    //Serial.println("State 5");
    //Serial.println("State 5");
      if (digitalRead(firePin)) {
        Commands.I = true;
        esp_err_t result = esp_now_send(broadcastAddress, (uint8_t *) &Commands, sizeof(Commands));
        if (result != ESP_OK) {
            break;
          // Serial.println("Sent with success");
          }
        //Commands.I = false;
       Commands.S1 = servo1OpenPosition;
       Commands.S2 = servo2OpenPosition;
        state = 0;
        result = esp_now_send(broadcastAddress, (uint8_t *) &Commands, sizeof(Commands));
        if (result != ESP_OK) {
            break;
          // Serial.println("Sent with success");
          }
        float now = millis();
        float runningTime = millis();
        digitalWrite(servo1Open, HIGH);
        digitalWrite(servo2Open, HIGH);
        while ((runningTime - now) <= 3000) {
          runningTime = millis();
          Serial.print(millis());
  Serial.print(" ");
  Serial.print(incomingPT1);
  Serial.print(" ");
  Serial.print(incomingPT2);
  Serial.print(" ");
  Serial.print(incomingPT3);
  Serial.print(" ");
  Serial.print(incomingPT4);
  Serial.print(" ");
  Serial.print(incomingLC1);
  Serial.print(" ");
  Serial.print(incomingLC2);
  Serial.print(" ");
  Serial.print(incomingLC3);
  Serial.print(" ");
  Serial.print(incomingFM);
  Serial.print(" ");
  Serial.print(Commands.S1);
  Serial.print(" ");
  Serial.print(Commands.S2);
  Serial.print(" ");
  Serial.print(Commands.I);
  Serial.print(" ");
  Serial.println(Commands.S1S2);
        }
        digitalWrite(servo1Open, LOW);
        Commands.S1 = servo1ClosedPosition;
        result = esp_now_send(broadcastAddress, (uint8_t *) &Commands, sizeof(Commands));
        if (result != ESP_OK) {
            break;
          // Serial.println("Sent with success");
          }
        now = millis();
        runningTime = millis();
        while ((runningTime - now) <= 500) {
          runningTime = millis();
          Serial.print(millis());
  Serial.print(" ");
  Serial.print(incomingPT1);
  Serial.print(" ");
  Serial.print(incomingPT2);
  Serial.print(" ");
  Serial.print(incomingPT3);
  Serial.print(" ");
  Serial.print(incomingPT4);
  Serial.print(" ");
  Serial.print(incomingLC1);
  Serial.print(" ");
  Serial.print(incomingLC2);
  Serial.print(" ");
  Serial.print(incomingLC3);
  Serial.print(" ");
  Serial.print(incomingFM);
  Serial.print(" ");
  Serial.print(Commands.S1);
  Serial.print(" ");
  Serial.print(Commands.S2);
  Serial.print(" ");
  Serial.print(Commands.I);
  Serial.print(" ");
  Serial.println(Commands.S1S2);
        }
        Commands.S2 = servo2ClosedPosition;
         result = esp_now_send(broadcastAddress, (uint8_t *) &Commands, sizeof(Commands));
        if (result != ESP_OK) {
            break;
          // Serial.println("Sent with success");
          }
        digitalWrite(servo2Open, LOW);
      }
      if (digitalRead(buttonpin1)) {
        state = 0;
      }
      if ((millis() - receiveTimeDAQ) > 50) {
        digitalWrite(DAQIndicator, LOW);
      }
      if ((millis() - receiveTimeCOM) > 50) {
        digitalWrite(COMIndicator, LOW);
      }

    delay(30);
  }

  Serial.print(millis());
  Serial.print(" ");
  Serial.print(incomingPT1);
  Serial.print(" ");
  Serial.print(incomingPT2);
  Serial.print(" ");
  Serial.print(incomingPT3);
  Serial.print(" ");
  Serial.print(incomingPT4);
  Serial.print(" ");
  Serial.print(incomingLC1);
  Serial.print(" ");
  Serial.print(incomingLC2);
  Serial.print(" ");
  Serial.print(incomingLC3);
  Serial.print(" ");
  Serial.print(incomingFM);
  Serial.print(" ");
  Serial.print(Commands.S1);
  Serial.print(" ");
  Serial.print(Commands.S2);
  Serial.print(" ");
  Serial.print(Commands.I);
  Serial.print(" ");
  Serial.println(Commands.S1S2);

  esp_err_t result = esp_now_send(broadcastAddress, (uint8_t *) &Commands, sizeof(Commands));


}

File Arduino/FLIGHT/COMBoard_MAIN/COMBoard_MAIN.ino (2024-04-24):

/*
This code runs on the COM ESP32 and has a couple of main tasks.
1. Receive sensor data from DAQ ESP32
2. Send servo commands to DAQ ESP32
*/

#include <esp_now.h>
#include <WiFi.h>
#include <Wire.h>
#include <Arduino.h>
#include "HX711.h"
#include <Ra01S.h>
//#include <ezButton.h>
#include "avdweb_Switch.h"
#include "freertos/FreeRTOS.h"
#include "freertos/Task.h"

#define COM_ID 0
#define DAQ_ID 1
#define FLIGHT_ID 2

//IF YOU WANT TO DEBUG, SET THIS TO True, if not, set False
bool DEBUG = false;
bool WIFIDEBUG = false;
bool SWITCHES = false; // If we are using switches

Switch SWITCH_ARMED = Switch(14);  //correct
Switch SWITCH_PRESS = Switch(12);  //correct
Switch SWITCH_QD = Switch(26);   //  correct
Switch SWITCH_IGNITION = Switch(21);
Switch SWITCH_HOTFIRE = Switch(23);
Switch SWITCH_ABORT = Switch(18);
#define LED_ARMED 13   //correct
#define LED_PRESSETH 25 //correct
#define LED_PRESSLOX 33 //corect
#define LED_PRESS 32 //correct
#define LED_QD 27 //correct
#define LED_IGNITION 19 //
#define LED_HOTFIRE 22  //correct
#define LED_ABORT 5

// LORA PARAMETERS
#define RF_FREQUENCY                                915000000 // Hz  center frequency
#define TX_OUTPUT_POWER                             22        // dBm tx output power
#define LORA_SPREADING_FACTOR                       7         // spreading factor [SF5..SF12]
#define LORA_BANDWIDTH                              4         // bandwidth
                                                              // 2: 31.25Khz
                                                              // 3: 62.5Khz
                                                              // 4: 125Khz
                                                              // 5: 250KHZ
                                                              // 6: 500Khz 
#define LORA_CODINGRATE                             1         // [1: 4/5,
                                                              //  2: 4/6,
                                                              //  3: 4/7,
                                                              //  4: 4/8]

#define LORA_PREAMBLE_LENGTH                        8         // Same for Tx and Rx
#define LORA_PAYLOAD_LENGTH                          0         // 0: Variable length packet (explicit header)
                                                              // 1..255  Fixed length packet (implicit header)
SX126x  loraModule(15,               //Port-Pin Output: SPI select
             21,               //Port-Pin Output: Reset 
             39               //Port-Pin Input:  Busy
             );


esp_now_peer_info_t peerInfo;

enum STATES {IDLE, ARMED, PRESS, QD, IGNITION, HOTFIRE, ABORT};
String stateNames[] = { "Idle", "Armed", "Press", "QD", "Ignition", "HOTFIRE", "Abort" };

//#define DEBUG_IDLE 90
//#define DEBUG_ARMED 91
//#define DEBUG_PRESS 92
//#define DEBUG_QD 93
//#define DEBUG_IGNITION 94
//#define DEBUG_HOTFIRE 95
//#define DEBUG_ABORT 96

//ENSURE MAC ADDRESS IS CORRECT FOR DEVICE IN USE!!!
//DAQ Breadboard {0x24, 0x62, 0xAB, 0xD2, 0x85, 0xDC}
//DAQ Protoboard {0x0C, 0xDC, 0x7E, 0xCB, 0x05, 0xC4}
//NON BUSTED DAQ {0x7C, 0x9E, 0xBD, 0xD8, 0xFC, 0x14}
// {0xC4, 0xDD, 0x57, 0x9E, 0x96, 0x34};
// uint8_t broadcastAddress[] = {0xC8, 0xF0, 0x9E, 0x50, 0x23, 0x34}; //Core board 1
//uint8_t broadcastAddress[] = {0x08, 0x3A, 0xF2, 0xB7, 0xEE, 0x00}; //TEST
//{0x30, 0xC6, 0xF7, 0x2A, 0x28, 0x04}

uint8_t DAQBroadcastAddress[] = {0xE8, 0x6B, 0xEA, 0xD3, 0x93, 0x88};
//uint8_t FlightBroadcastAddress[] = {0x48, 0x27, 0xE2, 0x2C, 0x80, 0xD8}; //CORE 1 V2
uint8_t FlightBroadcastAddress[] = {0x34, 0x85, 0x18, 0x71, 0x06, 0x60}; //CORE 3 V2

//Structure example to send data
//Must match the receiver structure
struct struct_readings {
  float PT_O1;
  float PT_O2;
  float PT_E1;
  float PT_E2;
  float PT_C1;
  float PT_X;
  float TC_1;
  float TC_2;
  float TC_3;
  float TC_4;
};

struct struct_message {
  int messageTime;
  int sender;
  int COMState;
  int DAQState;
  int FlightState;
  bool AUTOABORT;

  short int FlightQueueLength;
  bool ethComplete;
  bool oxComplete;
  bool oxVentComplete;
  bool ethVentComplete;
  bool sdCardInitialized;

  struct_readings filteredReadings;
  struct_readings rawReadings;
};

// Create a struct_message called Readings to recieve sensor readings remotely
struct_message incomingDAQReadings;
struct_message incomingFlightReadings;
// Create a struct_message to send commands
struct_message sendCommands;

int COMState = IDLE;
int DAQState = IDLE;
int FlightState = IDLE;

void setup() {
  // put your setup code here, to run once:
  Serial.begin(115200);
  Serial.println("Start of Setup");

  // setup LEDs and set to LOW
  pinMode(LED_ARMED, OUTPUT);
  pinMode(LED_PRESSETH, OUTPUT);
  pinMode(LED_PRESSLOX, OUTPUT);
  pinMode(LED_PRESS, OUTPUT);
  pinMode(LED_QD, OUTPUT);
  pinMode(LED_IGNITION, OUTPUT);
  pinMode(LED_HOTFIRE, OUTPUT);
  pinMode(LED_ABORT, OUTPUT);

  digitalWrite(LED_ARMED, LOW);
  digitalWrite(LED_PRESSETH, LOW);
  digitalWrite(LED_PRESSLOX, LOW);
  digitalWrite(LED_PRESS, LOW);
  digitalWrite(LED_QD, LOW);
  digitalWrite(LED_IGNITION, LOW);
  digitalWrite(LED_HOTFIRE, LOW);
  digitalWrite(LED_ABORT, LOW);


  Serial.println(WiFi.macAddress());
  //set device as WiFi station
  WiFi.mode(WIFI_STA);

  //initialize ESP32
  if (esp_now_init() != ESP_OK) {
    Serial.println("Error initializing ESP-NOW");
    return;
  }

  // Register peer
  peerInfo.channel = 0;
  peerInfo.encrypt = false;
  
  // Add peer
  memcpy(peerInfo.peer_addr, DAQBroadcastAddress, 6);

  if (esp_now_add_peer(&peerInfo) != ESP_OK){
    Serial.println("Failed to add peer");
  }

  memcpy(peerInfo.peer_addr, FlightBroadcastAddress, 6);
  
  if (esp_now_add_peer(&peerInfo) != ESP_OK){
    Serial.println("Failed to add peer");
    return;
  }

  Serial.print("My MAC Address ");
  Serial.println(WiFi.macAddress());

  // Register for a callback function that will be called when data is received
  esp_now_register_recv_cb(OnDataRecv);

  // Setup lora
  setupLora();

  COMState = IDLE;
}
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

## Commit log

2022-09-25 Move LE2 files over from ELLIE-ground
    [le2_ground.kicad_pcb, le2_ground.kicad_sch]
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2023-02-01 chjecks
    cheks
    [PTCalibration_Jan25_plsssss.xls]
2023-02-02 updates
    changed matlab files, org folders
    [PTCalibration_2.xls, PTCalibration_3.xls, PTCalibration_Oct29_newnew.xls]
2023-02-02 Working software
    [PT4_Cal.xls, PTCal_201.xls, PTCal_201_2.xls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]
2023-02-02 Cryo Test
    [res_data_2023-02-02_test4.csv, res_data_2023-02-02_test5.csv]
2023-02-03 RPA data
    rpa
    [Engine_Parameters.txt]
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2023-02-09 dlight adtkja
    [res_data_2023-02-08_test1.csv, res_data_2023-02-08_test2.csv]
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2023-02-13 daq pcb
    [le2-daq-new.kicad_pcb, le2-daq-new.kicad_sch]
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2023-03-11 pcb updates etc
    [le2-daq-new.kicad_pcb]
2023-03-11 skeleton pcbs
    [HX-board.kicad_pcb, HX-board.kicad_sch, TC-board.kicad_pcb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]
2023-03-14 Progress for TC board.
    [TC-board.kicad_sch]
2023-03-14 Updated TC-board schematics.
    [TC-board.kicad_pcb]
2023-03-15 CORE PCB DONE
    [le2-daq-new-B_Cu.gbr, le2-daq-new-B_Mask.gbr, le2-daq-new-B_Paste.gbr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]
2023-03-23 done with daq layout FRFRFRF
    [le2-daq-new.kicad_pcb, le2-daq-new.kicad_sch]
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2023-04-09 deleted unwanted files
    [CSD25402Q3A.step]
2023-04-13 DAQ datasend timing update
    timing fixed by resetting time at a time period not affected by function execution.
    [DAQBoard_LE2.ino, PTTest.ino]
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2023-04-15 daq pin updates (PT3 pin34 broken)
    [DAQBoard_LE2.ino]
2023-04-15 serial print formatted for csv file simplicity
    [serialplot_2023-04-15_test2.csv, serialplot_2023-04-15_test3.csv, serialplot_2023-04-15_test4.csv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]
2023-04-15 abort procedure fix and press(led off at repress)
    [COMBoard_LE2.ino, DAQBoard_LE2.ino]
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2023-06-13 analysis updates
    [Engine_Parameters.txt]
2023-06-20 reorganized simulation stuff
    [hotfire1_2023-04-16.xlsx, hotfire2_2023-04-16.xlsx]
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2023-08-05 Liquid flight sim
    [Alula_Cd_PowerOff.csv, Alula_Cd_PowerOn.csv]
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2023-10-06 random things plus calibration. Test 8 is accurate cal for hx2
    [testing_calibration_2023-10-05_test1.csv, testing_calibration_2023-10-05_test2.csv, testing_calibration_2023-10-05_test3.csv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]
2023-10-06 live plot updated
    [hotfire_cryo_test_serialplot_2023-04-16_test1.csv, hotfire_serialplot_2023-04-16_test1.csv, hotfire_serialplot_2023-04-16_test2.csv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]
2023-10-06 newww live
    [hotfire_cryo_test_serialplot_2023-04-16_test1.csv, hotfire_serialplot_2023-04-16_test1.csv, hotfire_serialplot_2023-04-16_test2.csv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]
2023-10-07 added daq delay
    [testing_2023-10-06_test1.csv, testing_2023-10-06_test10.csv, testing_2023-10-06_test11.csv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]
2023-10-07 Hotfire calibration
    [testing_calibration_2023-10-07_test1.csv, testing_calibration_2023-10-07_test10.csv, testing_calibration_2023-10-07_test11.csv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]
2023-10-13 small context changes
    [testing_calibration_2023-10-07_test27.csv]
2023-11-03 calibration org
    [testing_2023-10-06_test1.csv, testing_2023-10-06_test10.csv, testing_2023-10-06_test11.csv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]
2023-11-06 daq changes pii assignments for pcf
    [testing_calibration_2023-10-05_test8_CALHX1.csv, testing_calibration_2023-10-07_test1.csv, testing_calibration_2023-10-07_test10.csv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]
2023-11-07 pt calibration 11/7/23
    [PTCal_212.xls, PT_calibration_2023-11-07_2-5.csv, PT_calibration_2023-11-07_test1.csv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]
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2023-11-08 reverted to 5thNov commit to do mosfet testing, changed GPIO pins
    [DAQ_11-7-23.ino]
2023-11-14 11_13_2023 PT calibration
    [calibration_2023-11-13_HX1_C1_test1.csv, calibration_2023-11-13_HX1_C2_test2.csv, calibration_2023-11-13_HX2_C2_test1.csv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]
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2023-11-16 Com daq bug fixes with python gui
    [DAQ_11-13-23_filtered.ino]
2023-11-16 pt cal garage
    [(bad one)calibration_2023-11-13_HX1_C1_test1.csv, calibration_2023-11-16_HX2_C1.csv]
2023-11-16 Fixed pinouts from 11/15/23 testing
    [DAQ_11-13-23.ino, DAQ_11-13-23_filtered.ino]
2023-11-17 11/17 cal
    [2023-11-17_test2.csv]
2023-11-18 fix press valves staying on in debug
    [DAQ_11-13-23_filtered.ino]
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2023-11-18 added calibration, gain proper, and polyfit code
    [2023-11-17_test2.csv]
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2023-11-19 11/18 HOTFIRE DATA
    [HOTFIRE_2023-11-19_test4.csv]
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2023-11-19 Data from failed hotfire attempt 11/18
    [HOTFIRE_2023-11-18_test19.csv]
2023-11-26 analysis start
    [HOTFIRE_2023-11-19_test4.csv]
2023-11-27 excel cahnges
    [HOTFIRE_2023-11-18_test19.csv, HOTFIRE_2023-11-18_test19_FAILEDPRESS.xlsx, HOTFIRE_2023-11-19_test4.csv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]
2024-01-08 regen
    setup for dev, script setup
    [Regen_Scratch.xlsx]
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2024-02-09 mosfet fixes
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2024-02-10 updated abaort
    [HOTFIRE_2023-11-18_test19_FAILEDPRESS.xlsx, HOTFIRE_2023-11-19_test4_FULLRUN.xlsx]
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2024-02-13 new press() function that shouldnt stop pressing upon receiving a noise spike
    [DAQ_POWER.ino]
2024-02-13 timer fixes
2024-02-19 Adding calibration csvs
    [calibration_2024-02-13_test1.csv, calibration_2024-02-13_test2.csv, calibration_2024-02-13_test3.csv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]
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2024-02-28 calibration hx2
    [calibration_2024-02-28_test4.csv]
2024-02-28 power thresholds for lp test
    [testing_calibration_2023-10-05_test8_CALHX1.csv, testing_calibration_2023-10-07_test1.csv, testing_calibration_2023-10-07_test10.csv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]
2024-02-29 Leak Test + PT constants
    [DAQ_POWER.ino, DAQ_SENSE.ino]
2024-03-01 pressure flags
    [HOTFIRE_2024-03-01_test1.csv, HOTFIRE_2024-03-01_test2.csv]
2024-03-01 ETH/OX DONEEEE
    [HOTFIRE_2024-03-01_test3.csv, HOTFIRE_2024-03-01_test4.csv, HOTFIRE_2024-03-01_test5.csv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]
2024-03-02 com getting both power and sense source. currently reading sense
    [HOTFIRE_2024-03-01_test1.csv, HOTFIRE_2024-03-01_test2.csv, HOTFIRE_2024-03-01_test3.csv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]
2024-03-02 fixed constant wifi attempts
    [COMBoard_LE2_MAIN.ino]
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2024-03-05 Hotfire changes and updates to sense timing
    [calibration_2024-03-02_test16_edit.csv]
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2024-03-20 FlightBoard edits for abort actuation, name conventions
    [HOTFIRE_2024-02-10_test1.csv, calibration_2024-02-12_test1.csv, calibration_2024-02-12_test2.csv]
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2024-04-02 pt calibration pinouts updated
    [HOTFIRE_2024-02-10_test1.csv, HOTFIRE_2024-03-02_Pressure_Test.csv]
2024-04-10 fixed autoabort delay, and tested 3-way comm structure
    [DAQ.ino, FlightBoard.ino]
2024-04-16 SD card doesn't write in Idle now
    [FlightBoard.ino]
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2024-04-19 offset reset during idle initiate
    [calibration_2024-02-12_test1.csv, calibration_2024-02-12_test2.csv, calibration_2024-04-19_test12.csv]
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2024-04-21 extra PT, maybe fixed pin 5 issue?
    [DAQ.ino, FlightBoard.ino]
2024-04-21 com flight issues fixed
    [FlightBoard.ino]
2024-04-22 DAQ COM communication not working rn, COM Flight mostly works but won't return to idle
    [COMBoard_MAIN.ino, FlightBoard.ino]
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2024-04-23 Update DAQ.ino
    Fixed DAQ Code
    [DAQ.ino]
2024-04-23 debug cleanup, correct send signature assignment
    [FlightBoard.ino]
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
